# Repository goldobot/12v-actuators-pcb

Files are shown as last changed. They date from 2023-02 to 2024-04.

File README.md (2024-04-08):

# 12v-actuators-pcb
 Carte pour les actuateurs pneumatiques + capteur, moteurs brushless, répartition 12V et arrêt d'urgence du robot l'équipe Goldorak.
 
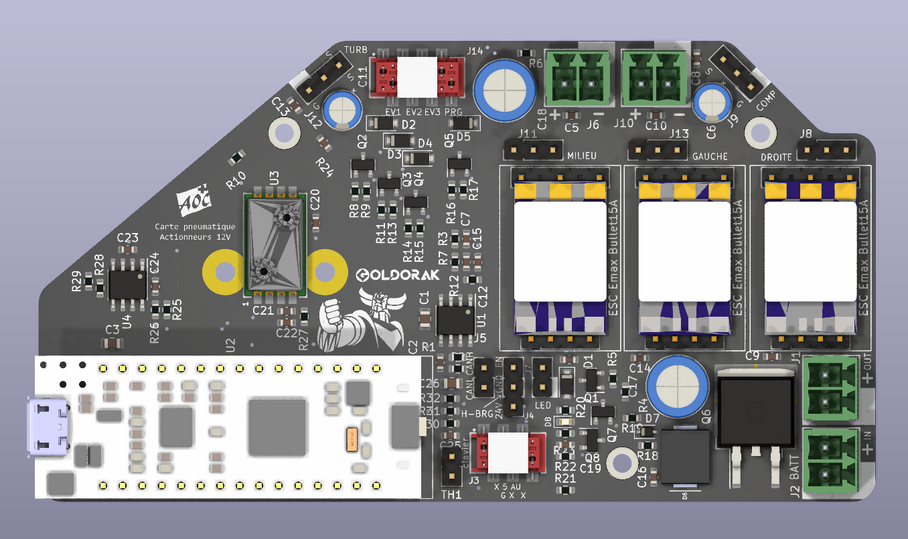
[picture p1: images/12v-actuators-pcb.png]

carte_12v_pneuma

## Specs composants carte actionneurs 12V
- Fuse holder keystone 3557-2
- D2PAK for p-channel mosfet ( https://fr.rs-online.com/web/p/transistors-mosfet/7105014 )
- STM32 uC: STM32F042K6 MCU sur carte de développement compatible pinout Arduino Nano
- 3 esc modules on board 15A
- 2 esc 35 off-board signal + alim, connecteur imposé
- Capteurs de pression, double emprunte
- Passer le 12V au pont en H, connecteur imposé
- Entrée NTC 100k piston compresseur -> uC
- 3 sorties électrovannes + 1 sortie purge

## Specs générales
- Tout doit être en Français de préférence
- Passer de Batt\_12V\_P à PWR12 avec fusible + arrêt d'urgence
- 5V fourni en externe (a découpler) + common mode choke?
- Échéance du draft le dimanche 26 février

## Taille de la PCB

Estimation                 |  Comparaison avec une carte bancaire
:-------------------------:|:-------------------------:
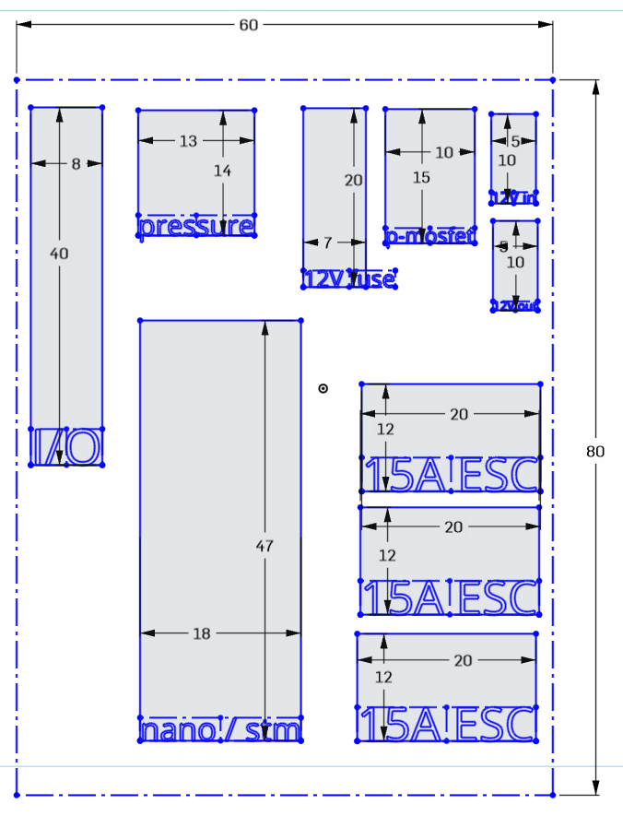
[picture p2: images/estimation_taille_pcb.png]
  |  

_Dimensions en mm_

## Place dans l'architecture générale
Voir "Carte pneumatique", milieu-droite.
carte pneuma dans l'architecture générale

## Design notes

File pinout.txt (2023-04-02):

PIN 1.1  : DS_M1
PIN 1.2  : N.C
PIN 1.3  : N.C
PIN 1.4  : N.C
PIN 1.5  : CAN_TD
PIN 1.6  : N.C
PIN 1.7  : SDA
PIN 1.8  : SCL
PIN 1.9  : DS_M2
PIN 1.10 : EV_P
PIN 1.11 : AU_STATUS
PIN 1.12 : DS_M3
PIN 1.13 : CAN_RD
PIN 1.14 : LCD_EN
PIN 1.15 : LED_EN

PIN 2.1  : VIN
PIN 2.2  : GND
PIN 2.3  : N.C
PIN 2.4  : N.C
PIN 2.5  : N.C
PIN 2.6  : EV_1
PIN 2.7  : DS_TURB
PIN 2.8  : DS_COMP
PIN 2.9  : EV_2
PIN 2.10 : EV_3
PIN 2.11 : A_PRES
PIN 2.12 : A_TEMP
PIN 2.13 : N.C
PIN 2.14 : 3V3
PIN 2.15 : N.C

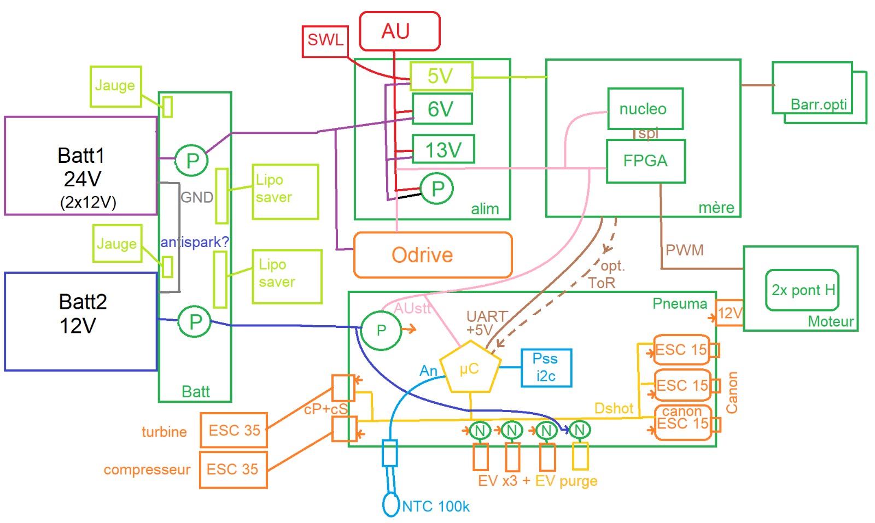
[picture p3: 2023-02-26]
images/goldorak_elec_architecture.jpeg

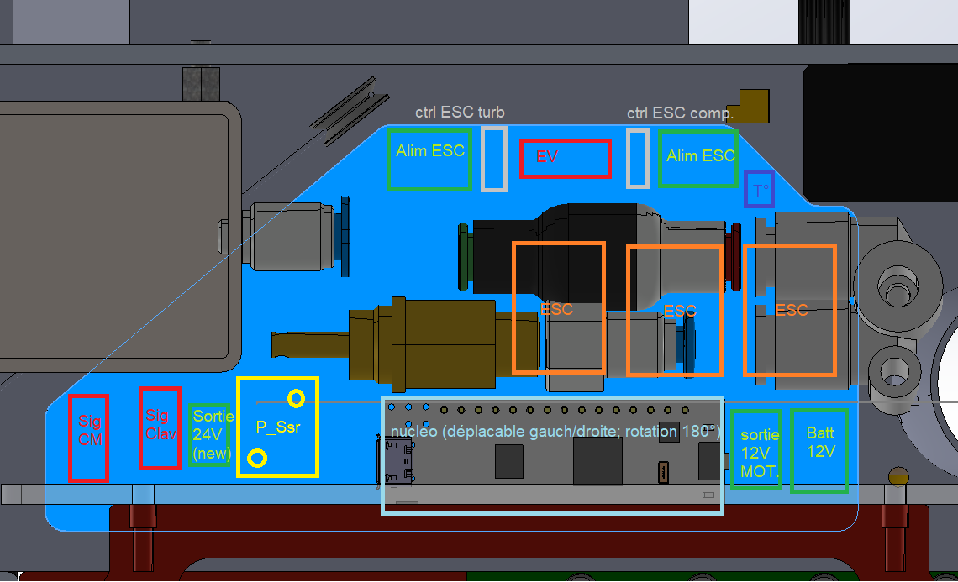
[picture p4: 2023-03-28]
images/estimation_finale_taille_pcb.png

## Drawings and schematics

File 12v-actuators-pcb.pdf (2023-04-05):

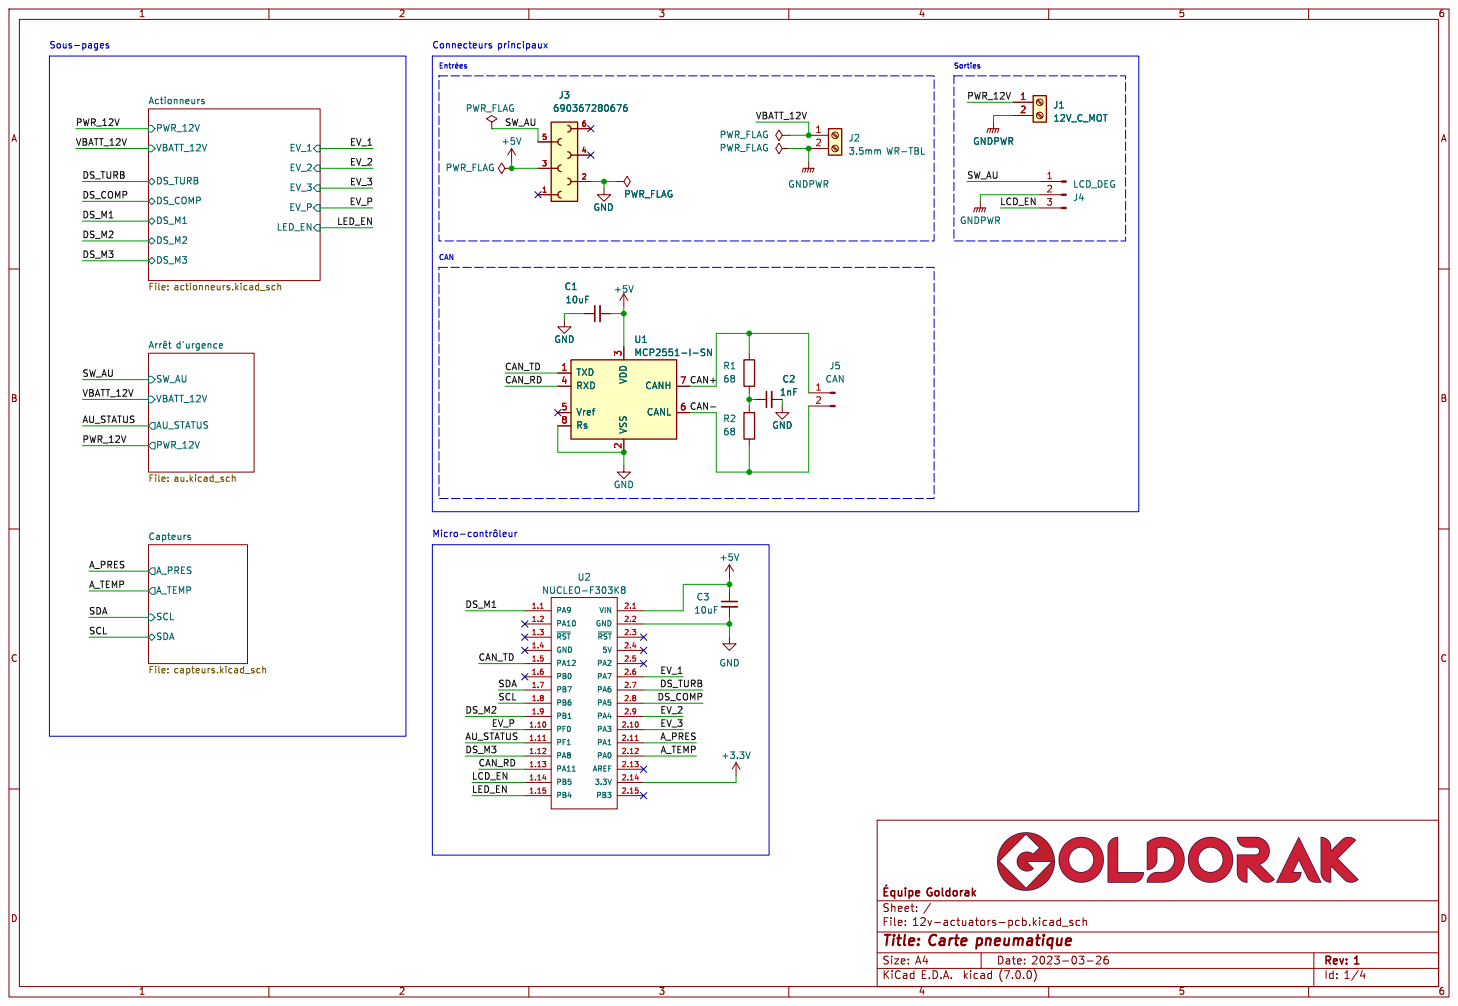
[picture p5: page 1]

þÿArrêt d'urgence File: au.kicad_sch PWR_12V
3.5mm WR-TBL C3

3 RXD 4 Vref 5 CANL 6 CANH 7 Rs 8 U1 MCP2551-I-SN

3 RXD 4 Vref 5 CANL 6 CANH 7 Rs 8 C2

File: 12v-actuators-pcb.kicad_sch Sheet: / þÿÉquipe Goldorak

Id: 1/4 Title: Carte pneumatique

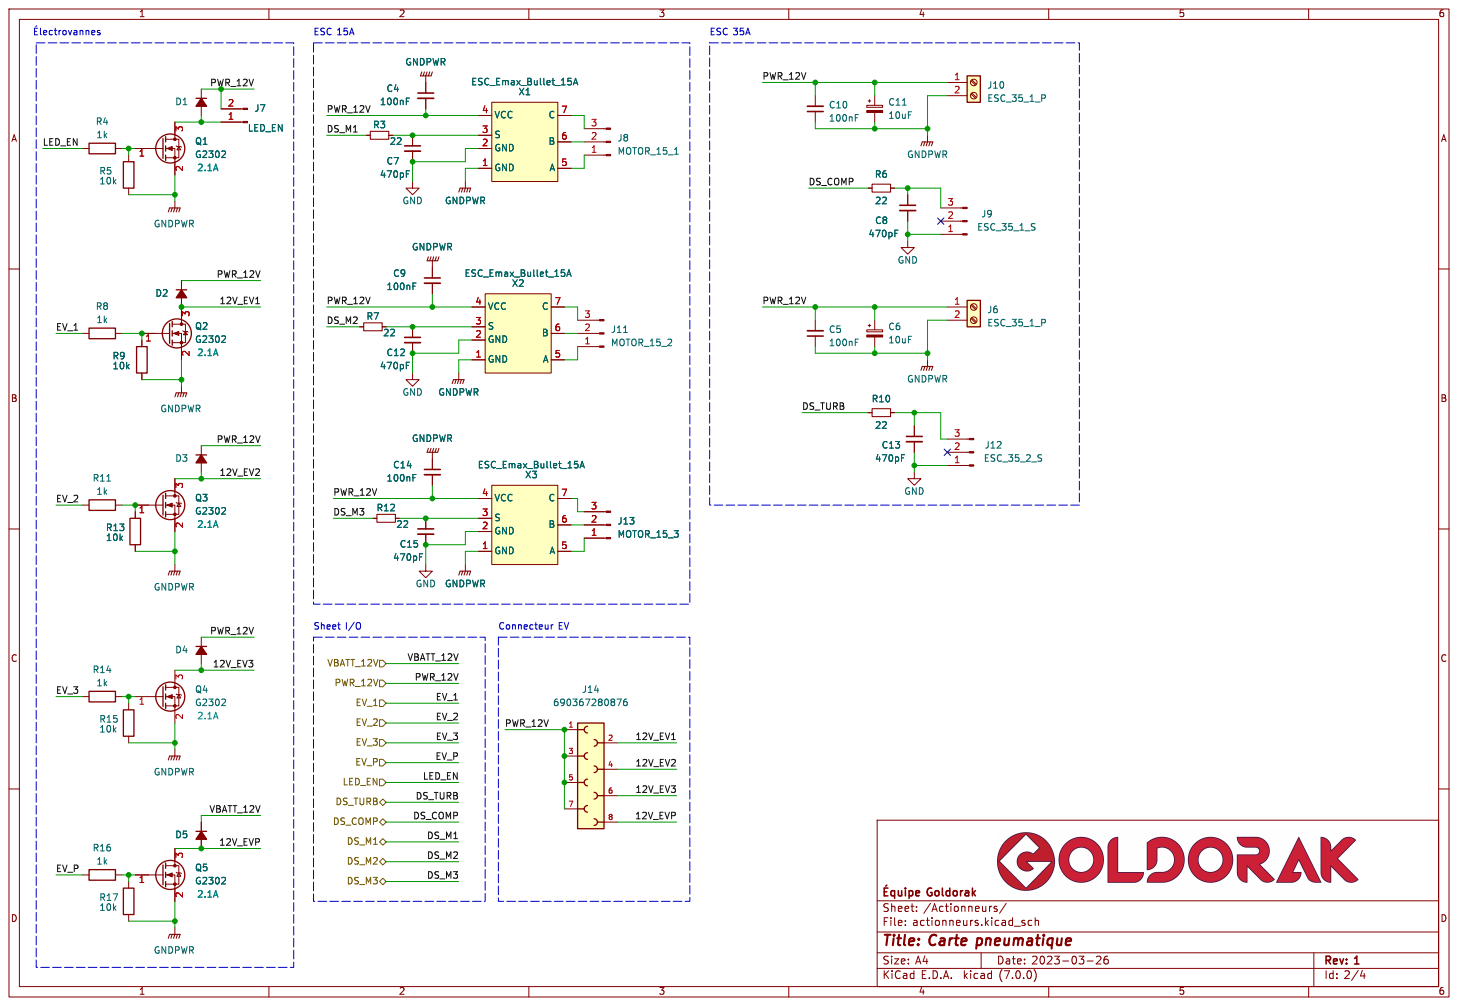
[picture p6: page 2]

File: actionneurs.kicad_sch Sheet: /Actionneurs/ þÿÉquipe Goldorak

Id: 2/4 Title: Carte pneumatique

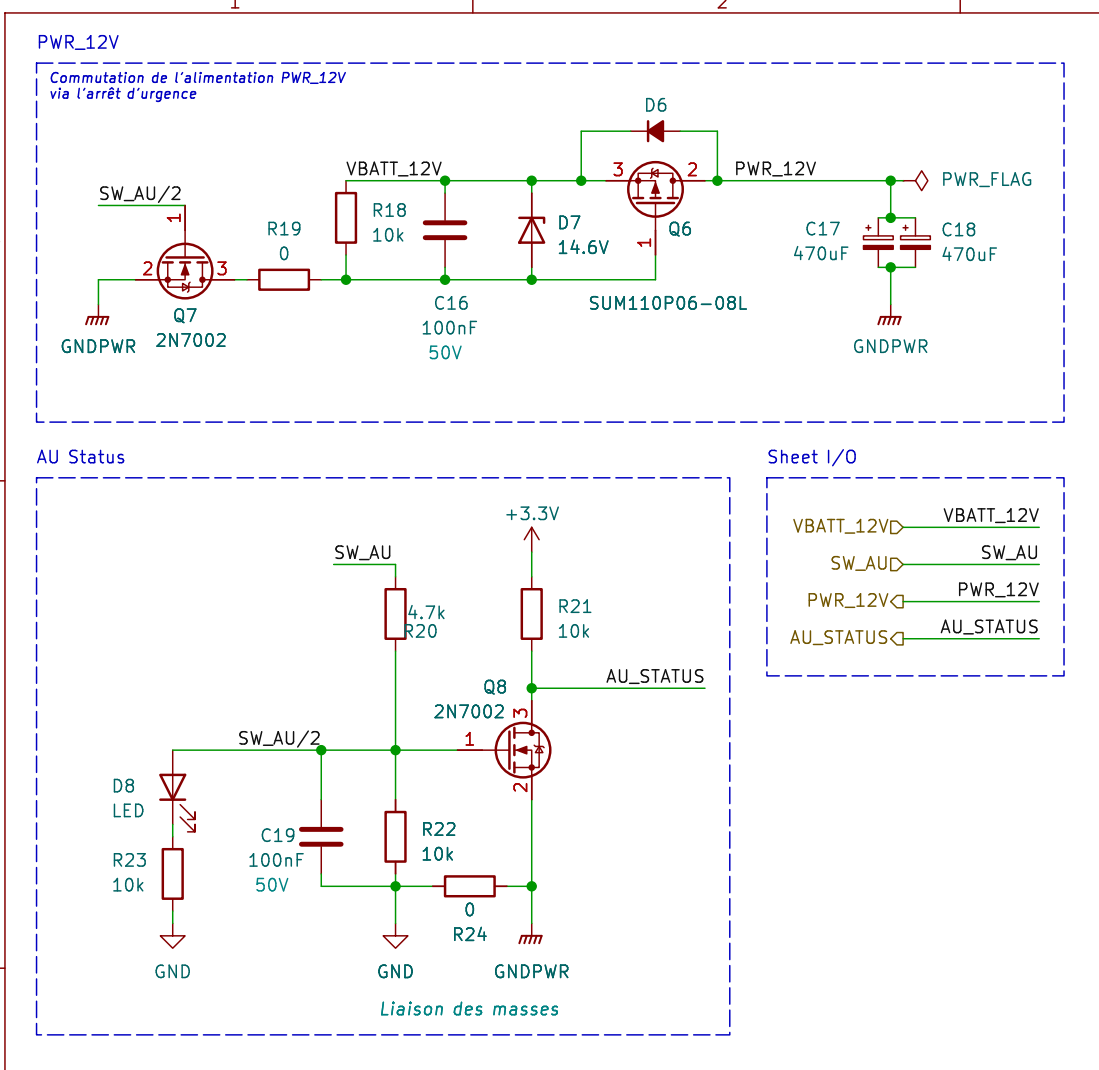
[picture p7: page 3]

þÿÉquipe Goldorak
File: au.kicad_sch Sheet: þÿ/Arrêt d'urgence/
Id: 3/4 Title: Carte pneumatique

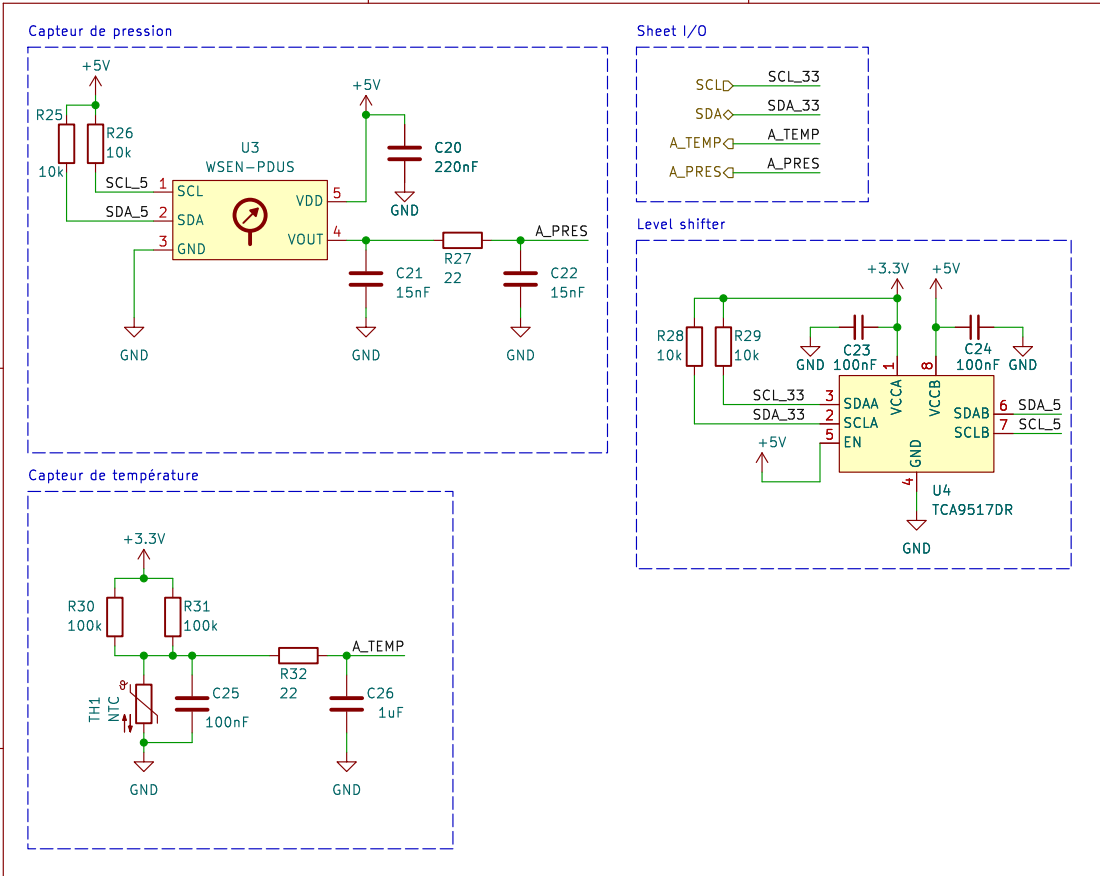
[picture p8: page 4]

4 EN 5 SDAB 6 SCLB 7 VCCB GND 8

4 EN 5 SDAB 6 SCLB 7 VCCB

þÿÉquipe Goldorak
File: capteurs.kicad_sch Sheet: /Capteurs/
Id: 4/4 Title: Carte pneumatique

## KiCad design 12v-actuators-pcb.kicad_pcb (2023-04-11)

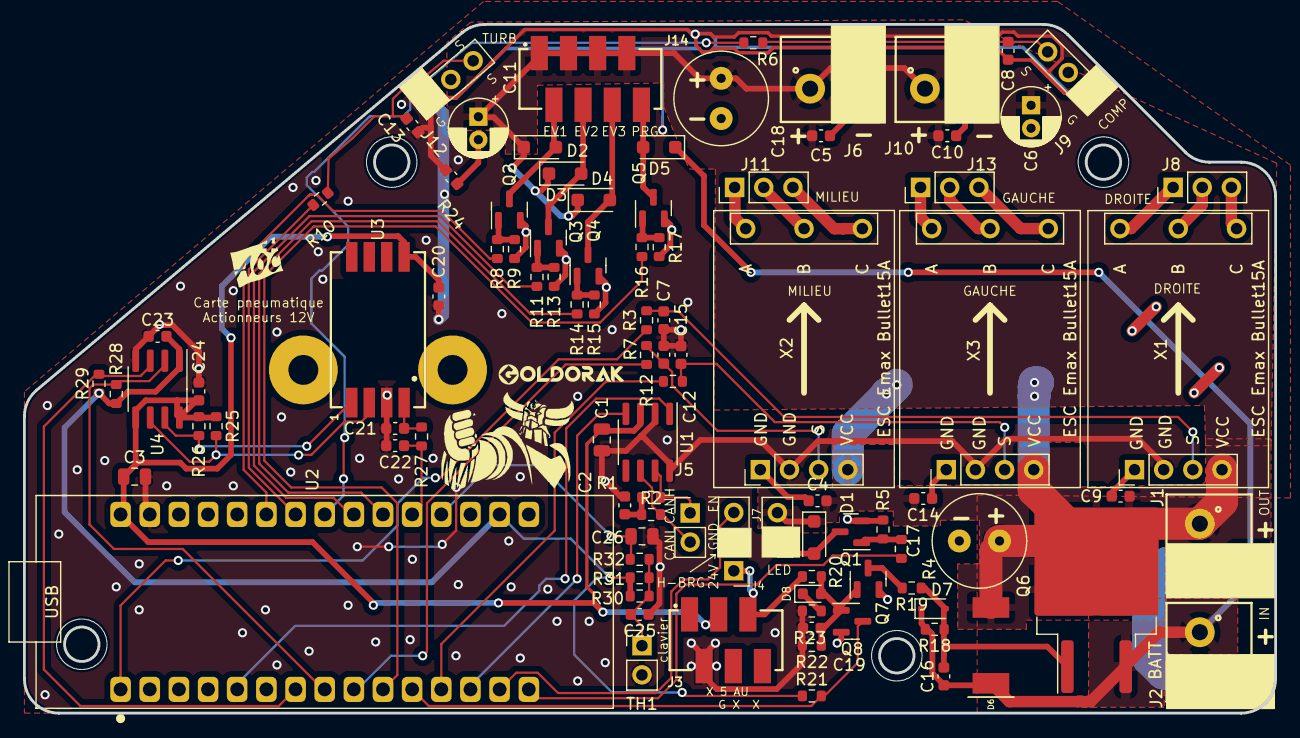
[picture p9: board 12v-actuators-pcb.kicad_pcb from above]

Board: 2 copper layers, 109.0 x 60.0 mm, 96 parts (0 on the bottom side), 60 nets.

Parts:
C1, C3: 10uF; C_0805_2012Metric
C2: 1nF; C_0603_1608Metric
C4, C5, C9, C10, C14, C16, C19, C23, C24, C25: 100nF; C_0603_1608Metric
C6, C11: 10uF; CP_Radial_D5.0mm_P2.00mm
C7, C8, C12, C13, C15: 470pF; C_0603_1608Metric
C17, C18: 470uF; C_Radial_D8.0mm_H11.5mm_P3.50mm
C20: 220nF; C_0603_1608Metric
C21, C22: 15nF; C_0603_1608Metric
C26: 1uF; C_0805_2012Metric
D1, D2, D3, D4, D5: D_SOD-123F
D6: DO-214AB
D7: 14.6V; D_SOD-323
D8: LED; LED_0603_1608Metric
J1: 12V_C_MOT; 691321100002
J2: 3.5mm WR-TBL; 691321100002
J3: 690367280676
J4: LCD_DEG; PinHeader_1x03_P2.54mm_Vertical
J5: CAN; PinHeader_1x02_P2.54mm_Vertical
J6: ESC_35_1_P; 691321100002
J7: LED_EN; PinHeader_1x02_P2.54mm_Vertical
J8: MOTOR_15_1; PinHeader_1x03_P2.54mm_Vertical
J9: ESC_35_1_S; PinHeader_1x03_P2.54mm_Vertical
J10: ESC_35_2_P; 691321100002
J11: MOTOR_15_2; PinHeader_1x03_P2.54mm_Vertical
J12: ESC_35_2_S; PinHeader_1x03_P2.54mm_Vertical
J13: MOTOR_15_3; PinHeader_1x03_P2.54mm_Vertical
J14: 690367280876
Q1, Q2, Q3, Q4, Q5: G2302; SOT-23
Q6: SUM110P06-08L; TO-263-2
Q7, Q8: 2N7002; SOT-23
R1, R2: 68; R_0603_1608Metric
R3, R6, R7, R10, R12, R27, R32: 22; R_0603_1608Metric
R4, R8, R11, R14, R16: 1k; R_0603_1608Metric
R5, R9, R13, R15, R17, R18, R21, R22, R23, R25, R26, R28, R29: 10k; R_0603_1608Metric
R19: 0; R_0603_1608Metric
R20: 4.7k; R_0603_1608Metric
R24: 0; C_0603_1608Metric
R30, R31: 100k; R_0603_1608Metric
TH1: NTC; PinHeader_1x02_P2.54mm_Vertical
U1: MCP2551-I-SN; SOIC-8_3.9x4.9mm_P1.27mm
U2: NUCLEO-F303K8; MODULE_NUCLEO-F303K8
U3: WSEN-PDUS; WSEN-PDUS_2513130810X01
U4: TCA9517DR; SOIC-8_3.9x4.9mm_P1.27mm
X1, X2, X3: ESC_Emax_Bullet_15A

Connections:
+3.3V: C23.1, R21.1, R28.1, R29.1, R30.1, R31.1, U2.2.14 (3.3V), U4.1 (VCCA)
+5V: C1.2, C3.1, C20.1, C24.1, J3.3, R25.1, R26.1, U1.3 (VDD), U2.2.1 (VIN), U3.5 (VDD), U4.5 (EN), U4.8 (VCCB)
/AU_STATUS: Q8.3 (D), R21.2, U2.1.11 (PF1)
/A_PRES: C22.1, R27.2, U2.2.11 (PA1)
/A_TEMP: C26.2, R32.2, U2.2.12 (PA0)
/Actionneurs/12V_EV1: D2.2 (A), J14.2, Q2.3 (D)
/Actionneurs/12V_EV2: D3.2 (A), J14.4, Q3.3 (D)
/Actionneurs/12V_EV3: D4.2 (A), J14.6, Q4.3 (D)
/Actionneurs/12V_EVP: D5.2 (A), J14.8, Q5.3 (D)
/Arrêt d'urgence/SW_AU/2: C19.1, D8.2 (A), Q7.1 (G), Q8.1 (G), R20.2, R22.2
/CAN+: J5.1, R1.1, U1.7 (CANH)
/CAN-: J5.2, R2.2, U1.6 (CANL)
/CAN_RD: U1.4 (RXD), U2.1.13 (PA11)
/CAN_TD: U1.1 (TXD), U2.1.5 (PA12)
/Capteurs/SCL_5: R26.2, U3.1 (SCL), U4.7 (SCLB)
/Capteurs/SDA_5: R25.2, U3.2 (SDA), U4.6 (SDAB)
/DS_COMP: R6.1, U2.2.8 (PA5)
/DS_M1: R3.1, U2.1.1 (PA9)
/DS_M2: R7.1, U2.1.9 (PB1)
/DS_M3: R12.1, U2.1.12 (PA8)
/DS_TURB: R10.1, U2.2.7 (PA6)
/EV_1: R8.2, U2.2.6 (PA7)
/EV_2: R11.2, U2.2.9 (PA4)
/EV_3: R14.2, U2.2.10 (PA3)
/EV_P: R16.2, U2.1.10 (PF0)
/LCD_EN: J4.3, U2.1.14 (PB5)
/LED_EN: R4.2, U2.1.15 (PB4)
/PWR_12V: C4.2, C5.2, C6.1, C9.2, C10.2, C11.1, C14.2, C17.1, C18.1, D1.1 (K), D2.1 (K), D3.1 (K), D4.1 (K), D6.2 (A), J1.1, J6.1, J7.2, J10.1, J14.1, J14.3, J14.5, J14.7, Q6.2 (D), X1.4 (VCC), X2.4 (VCC), X3.4 (VCC)
/SCL: R28.2, U2.1.8 (PB6), U4.2 (SCLA)
/SDA: R29.2, U2.1.7 (PB7), U4.3 (SDAA)
/SW_AU: J3.5, J4.1, R20.1
/VBATT_12V: C16.1, D5.1 (K), D6.1 (K), D7.1 (K), J2.1, Q6.3 (S), R18.2
GND: C1.1, C2.2, C3.2, C7.2, C8.2, C12.2, C13.2, C15.2, C19.2, C20.2, C21.2, C22.2, C23.2, C24.2, C25.1, C26.1, J3.2, J9.1, J12.1, R22.1, R23.2, R24.1, TH1.2, U1.2 (VSS), U1.8 (Rs), U2.2.2 (GND), U3.3 (GND), U4.4 (GND), X1.2 (GND), X2.2 (GND), X3.2 (GND)
GNDPWR: C4.1, C5.1, C6.2, C9.1, C10.1, C11.2, C14.1, C17.2, C18.2, J1.2, J2.2, J4.2, J6.2, J10.2, Q1.2 (S), Q2.2 (S), Q3.2 (S), Q4.2 (S), Q5.2 (S), Q7.2 (S), Q8.2 (S), R5.2, R9.2, R13.2, R15.2, R17.2, R24.2, X1.1 (GND), X2.1 (GND), X3.1 (GND)
unnamed: C2.1, R1.2, R2.1
unnamed: C25.2, R30.2, R31.2, R32.1, TH1.1
unnamed: D1.2 (A), J7.1, Q1.3 (D)
unnamed: C16.2, D7.2 (A), Q6.1 (G), R18.1, R19.1
unnamed: D8.1 (K), R23.1
unnamed: J8.1, X1.5 (A)
unnamed: J8.2, X1.6 (B)
unnamed: J8.3, X1.7 (C)
unnamed: C8.1, J9.3, R6.2
unnamed: J11.1, X2.5 (A)
unnamed: J11.2, X2.6 (B)
unnamed: J11.3, X2.7 (C)
unnamed: C13.1, J12.3, R10.2
unnamed: J13.1, X3.5 (A)
unnamed: J13.2, X3.6 (B)
unnamed: J13.3, X3.7 (C)
unnamed: Q1.1 (G), R4.1, R5.1
unnamed: Q2.1 (G), R8.1, R9.1
unnamed: Q3.1 (G), R11.1, R13.1
unnamed: Q4.1 (G), R14.1, R15.1
unnamed: Q5.1 (G), R16.1, R17.1
unnamed: Q7.3 (D), R19.2
unnamed: C21.1, R27.1, U3.4 (VOUT)
unnamed: C7.1, R3.2, X1.3 (S)
unnamed: C12.1, R7.2, X2.3 (S)
unnamed: C15.1, R12.2, X3.3 (S)

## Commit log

2023-02-26 Project start
    [12v-actuators-pcb.kicad_pcb, 12v-actuators-pcb.kicad_sch]
2023-02-26 Add 3.5mm header datasheet
2023-02-26 Ajout d'une comparaison de taille dans le README
2023-03-05 WIP: schematic begun
    [12v-actuators-pcb.kicad_sch]
2023-03-11 WIP: Arrêt d'urgence
    [12v-actuators-pcb.kicad_sch]
2023-03-14 Schéma AU fait + ESC + électrovannes débuté
    [12v-actuators-pcb.kicad_sch]
2023-03-22 Schematics mostly done, EV and ESC pins to validate with @MGMaximusk
    [12v-actuators-pcb.kicad_sch]
2023-03-22 Ajout du logo de l'équipe
    [12v-actuators-pcb.kicad_sch]
2023-03-26 Reorganize and finish schematic, assign footprints
    [12v-actuators-pcb.kicad_sch, actionneurs.kicad_sch, au.kicad_sch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]
2023-03-27 Correct CAN interface, add some filtering on sensors + add LCD board power connector
    [12v-actuators-pcb.kicad_sch, au.kicad_sch, capteurs.kicad_sch]
2023-03-27 Few details -> add filtering on 35A ESC signals + 3.3V capa ...
    [12v-actuators-pcb.kicad_sch, actionneurs.kicad_sch, au.kicad_sch]
2023-03-28 Schematics finished, reanotated sch
    [12v-actuators-pcb.kicad_pcb, 12v-actuators-pcb.kicad_sch, actionneurs.kicad_sch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]
2023-03-29 First placement draft
    [12v-actuators-pcb.kicad_pcb, capteurs.kicad_sch]
2023-04-01 Update schematic pinout for LED_EN + Add mechanical constraints to PCB layout
    [12v-actuators-pcb.kicad_pcb, 12v-actuators-pcb.kicad_sch, actionneurs.kicad_sch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]
2023-04-02 New PCB reorganisation around mechanical constraints
    [12v-actuators-pcb.kicad_pcb]
2023-04-04 Before making power planes
    Signal routing done. Added I2C level shifter in schematics.
    [12v-actuators-pcb.kicad_pcb, 12v-actuators-pcb.kicad_sch, actionneurs.kicad_sch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]
2023-04-05 PCB finished
    [12v-actuators-pcb.kicad_pcb, actionneurs.kicad_sch]
2023-04-05 reprise des plans et petite correction diverse
    [12v-actuators-pcb.kicad_pcb]
2023-04-05 oups, il manquait les fichiers proj et pcb
    [12v-actuators-pcb.kicad_pcb]
2023-04-05 Regenerate interactive BOM
    [12v-actuators-pcb.kicad_pcb]
2023-04-05 Update board 3D STEP files
